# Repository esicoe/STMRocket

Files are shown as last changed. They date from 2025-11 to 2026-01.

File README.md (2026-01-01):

# STMRocket (KiCad v9.0)

> An open source model rocket flight computer with datalogging & parachute deploying capabilities.
> 
<br>

**This project was sponsored and made possible by PCBWay**




<br>

## Project Description

This is a personal project for an STM32 flight computer that will be flown on a high-power rocket to achieve the Level 1 high power rocketry certification in Canada.
<br>

## Capabilities

The computer is able to store flight data from its two sensors:

- ICM42670: 6-axis IMU with a gyroscope and accelerometer
- BME280: Pressure, temperature and humidity sensor

Data from the accelerometer and gyroscope is used to activate the pyro charge and release the rocket's parachute (single-deploy configuration).

Flight data is stored in a 4-megabyte flash memory chip and is offloaded from the computer using MicroSD.
<br>

During flight, the computer is powered by a 2S LiPo battery through an XT30 connector.

Programming interfaces: SWD and USB Micro-B.

<br>

For a more detailed overview of the components, consult the BOM and the KiCad schematic.

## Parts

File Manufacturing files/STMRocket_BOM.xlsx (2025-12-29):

 |  |  | xxxx xxxx xxxxx xxPCS BOM (Sample Bill of Materials)
Item # | *Designator | *Qty | Manufacturer | *Mfg Part # | Description / Value | *Package/Footprint | Type | Your Instructions / Notes
1 | U1 | 1 | ST | STM32F103C8T6 | IC MCU 32BIT 64KB FLASH 48LQFP | LQFP-48 | SMD
2 | U2 | 1 | InvenSense | ICM-42670-P | IMU ACCEL/GYRO/TEMP I2C/SPI | LGA-14 | SMD
3 | U3 | 1 | Bosch | BME280 | SENSOR PRESSURE HUMIDITY TEMP | LGA-8 | SMD
4 | U4 | 1 | Renesas | AT25SF041B-SSHD-T | IC FLASH 4MBIT SPI/QUAD 8SOIC | SOIC-8 | SMD
5 | U5 | 1 | Nexperia | PESD3V3S4UD,115 | TVS DIODE 3.3VWM 12VC 6TSOP | TSOP-6 | SMD
6 | U6 | 1 | Diodes | AP63203WU | IC REG BUCK 3.3V 2A TSOT23-6 | TSOT-23-6 | SMD
7 | U7, U8 | 2 | TI | ESD122DMXR | TVS DIODE 3.6VWM 8.4VC 3X2SON | SON-6 | SMD
8 | U9 | 1 | Diodes | AZ1117CH2-3.3 | IC REG LINEAR 3.3V 1A SOT-223-3 | SOT-223-3 | SMD
9 | Y1 | 1 | ECS | ECS-2520MV-160-CN-TR | OSC XO 16.0000MHZ CMOS SMD | 4-SMD | SMD
10 | C1 | 1 | ChemiCon | EMVY350ARA470MF55G | CAP ALUM 47UF 20% 35V SMD | CP_Elec_6.3x5.2 | SMD
11 | C2,C3,C4 | 3 | TDK | C2012X5R1C106K085AC | CAP CER 10UF 16V X5R 0805 | 0805 | SMD
12 | C5,C6,C7,C8 | 4 | TDK | C1608X5R0J106K080AB | CAP CER 10UF 6.3V X5R 0603 | 0603 | SMD
13 | C9 | 1 | Samsung | CL10B225KP8NNNC | CAP CER 2.2UF 10V X7R 0603 | 0603 | SMD
14 | C10,C11,C12 | 3 | TDK | C1005X6S1C105K050EC | CAP CER 1UF 15V X6S 0402 | 0402 | SMD
15 | C13, C14, C15, C16, C17, C18, C19, C20, C21, C22, C23, C24, C25, C26, C27 | 15 | Samsung | CL10E104KC8VPNC | CAP CER 100NF 100V X8L 0603 | 0402 | SMD
16 | C28, C29 | 2 | Samsung | CL10B103KO8WPNC | CAP CER 10NF 16V X7R 0603 | 0402 | SMD
17 | D1 | 1 | Vishay | SMF5V0A-E3-08 | TVS DIODE 5VWM 9.2VC DO219AB | DO-219AB | SMD
18 | D2, D3, D4 | 3 | Littelfuse | SMF4L8.5AT1G | TVS DIODE 8.5VWM 14.4VC SOD123F | SOD-123F | SMD
19 | D5, D6 | 2 | Vishay | BZD27C3V6P-E3-08 | DIODE ZENER 3.6V 800MW DO219AB | DO-219AB | SMD
19 | D7 | 2 | Littelfuse | SMF3.3 | TVS DIODE 3.3VWM 6.8VC SOD123F | SOD-123F | SMD
20 | FB1 | 1 | Pulse | PE-0603PFB121ST | FERRITE BEAD 120 OHM 0603 1LN | 0603 | SMD
21 | J1 | 1 |  |  | XT30PW-M Horizontal Connector |  | DNS
22 | J2 | 1 | Amphenol | 10103594-0001LF | CONN RCPT USB2.0 MICRO B SMD R/A | USB Micro B | SMD
23 | J3 | 1 |  |  | Horizontal 01x02 Screw Terminal |  | DNS
24 | J4 | 1 |  |  | Horizontal 01x02 Pins |  | DNS
25 | J5 | 1 |  |  | Horizontal 01x04 Pins |  | DNS
26 | J6 | 1 | Wurth | 693072010801 | CONN MICRO SD CARD R/A SMD | MicroSD | SMD
27 | R1 | 1 | Yaego | RC0402FR-07100KL | RES 100K OHM 1% 1/16W 0402 | 0402 | SMD
28 | R2, R3, R4, R5, R6 | 5 | Yaego | RC0603FR-0710KL | RES 10K OHM 1% 1/10W 0603 | 0402 | SMD
29 | R7, R8 | 2 | Yaego | RC0402JR-074K7L | RES 4.7K OHM 5% 1/16W 0402 | 0402 | SMD
30 | R9 | 1 | Panasonic | ERA-2AEB152X | RES SMD 1.5K OHM 0.1% 1/16W 0402 | 0402 | SMD
31 | R10 | 1 | Caddock | MP930-2.00-1% | RES 2 OHM 1% 30W TO220 | TO-220 | DNS

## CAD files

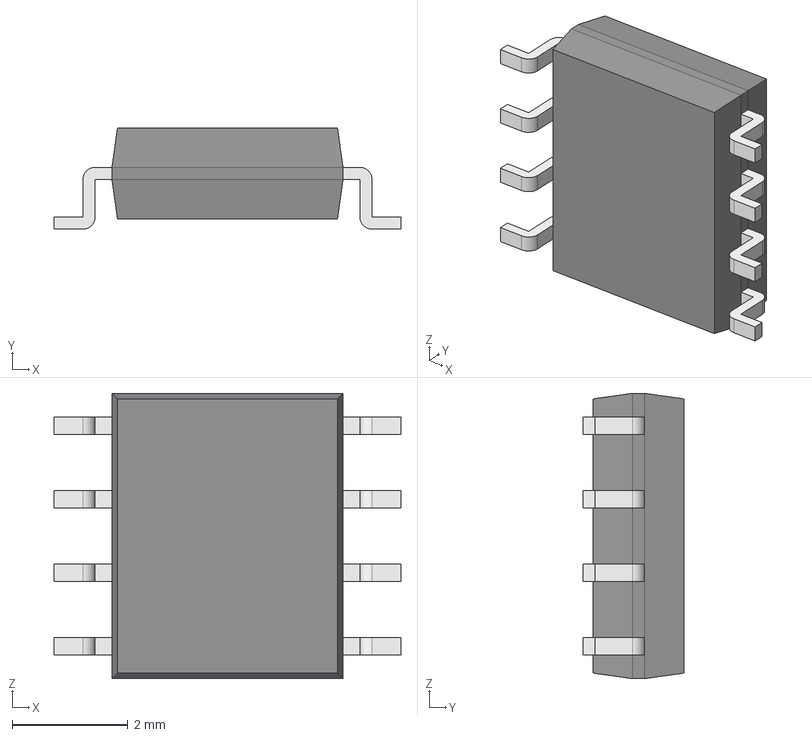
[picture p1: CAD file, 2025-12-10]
EDA files/EDA libraries/AT25SF041B-SSHD-T/AT25SF041B-SSHD-T.step
5.99 x 1.75 x 4.92 mm
Body001 (Mirror #1) x 4
XY-plane x 12
X-axis x 12

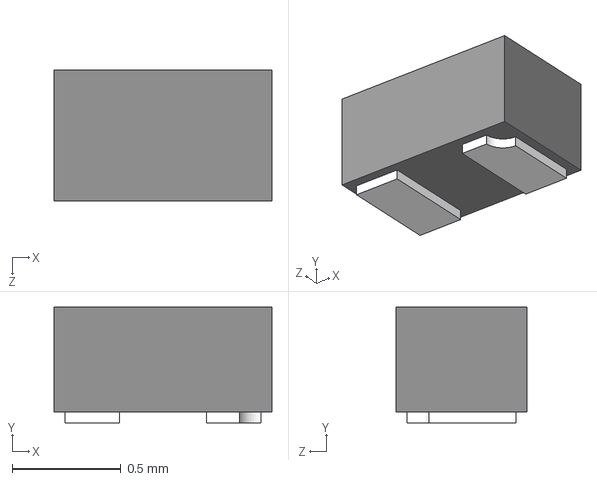
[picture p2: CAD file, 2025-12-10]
EDA files/EDA libraries/D12V0H1U2LP-7B/D12V0H1U2LP-7B.step
1.00 x 0.53 x 0.6 mm

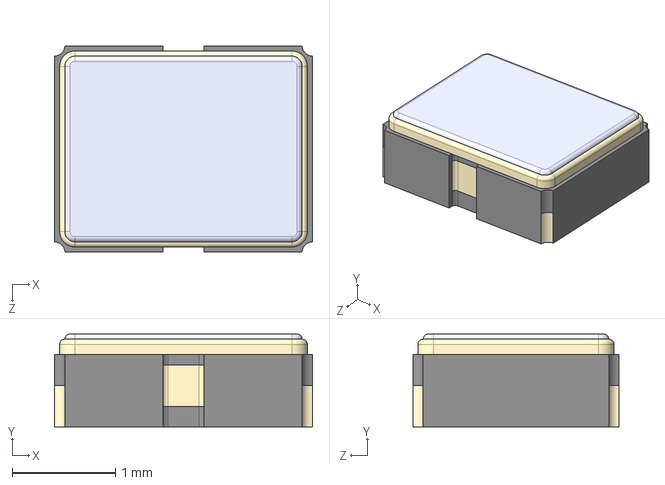
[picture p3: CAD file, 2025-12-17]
EDA files/EDA libraries/ECS-2520MV-160-CN-TR/ECS-2520MV-160-CN-TR.STEP
2.50 x 0.9 x 2.00 mm

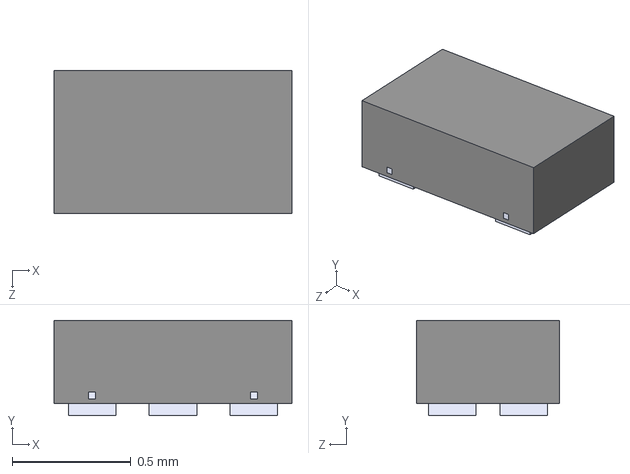
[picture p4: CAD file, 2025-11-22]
EDA files/EDA libraries/ESD122DMXR/ESD122DMXR.step
1.00 x 0.4 x 0.6 mm

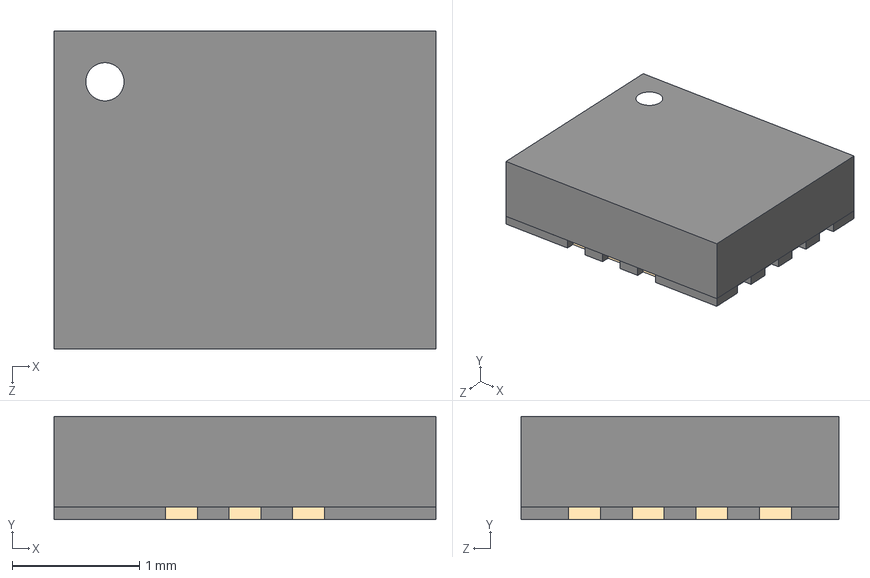
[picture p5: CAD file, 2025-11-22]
EDA files/EDA libraries/ICM_42670_P/ICM-42670-P.step
3.00 x 0.81 x 2.50 mm

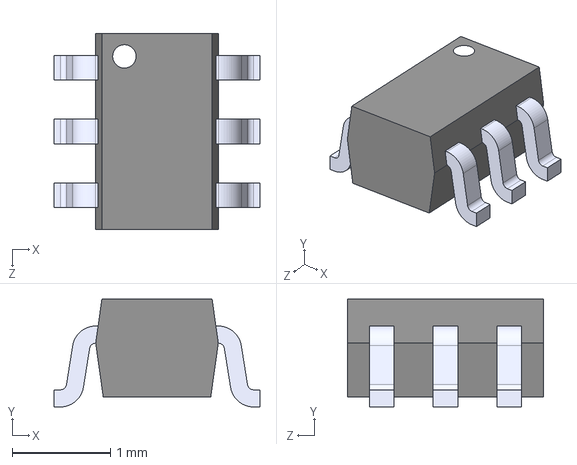
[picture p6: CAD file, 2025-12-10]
EDA files/EDA libraries/PESD3V3S5UD/PESD3V3S5UD.step
2.10 x 1.10 x 2.00 mm

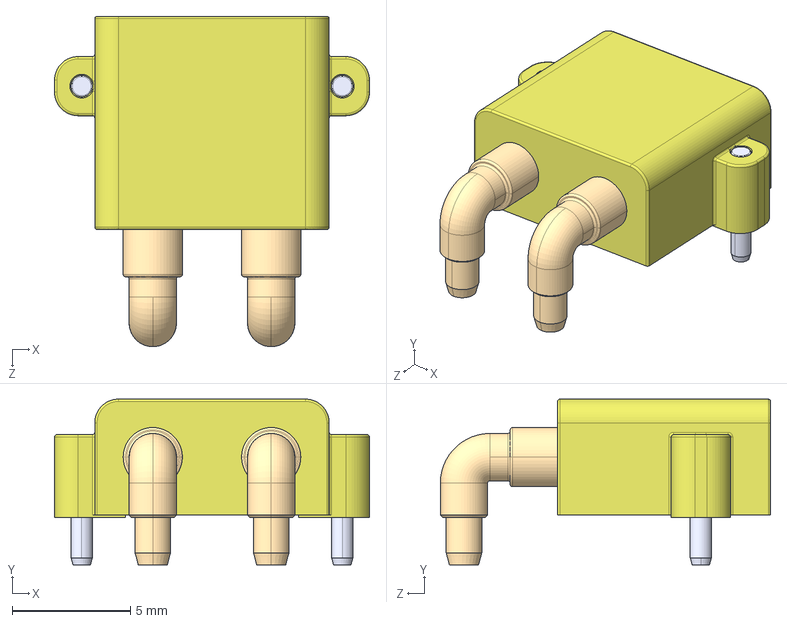
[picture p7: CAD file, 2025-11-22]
EDA files/EDA libraries/XT30PW-M/XT30PW-M--3DModel-STEP-269445.STEP
13.3 x 7.00 x 14.0 mm

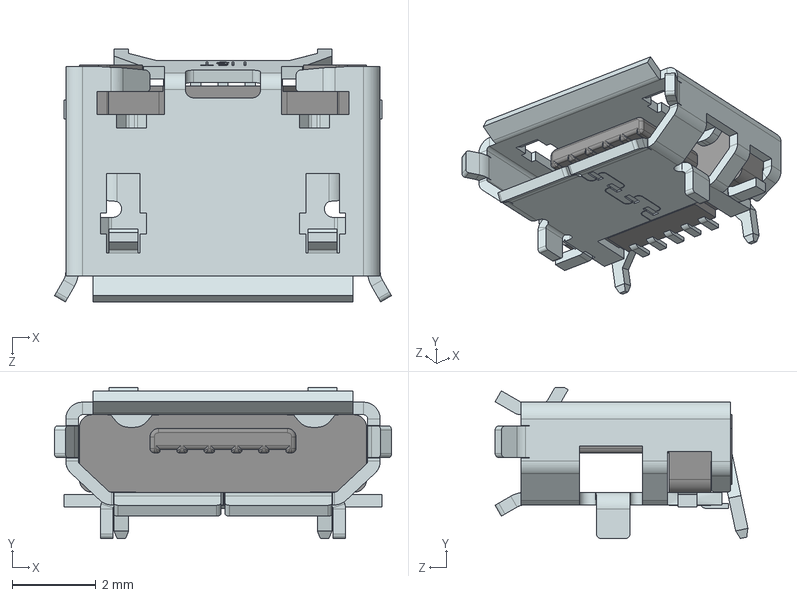
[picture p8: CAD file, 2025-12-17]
EDA files/EDA libraries/10103594-0001LF/10103594-0001LF--3DModel-STEP-269445.STEP
8.04 x 3.60 x 6.03 mm

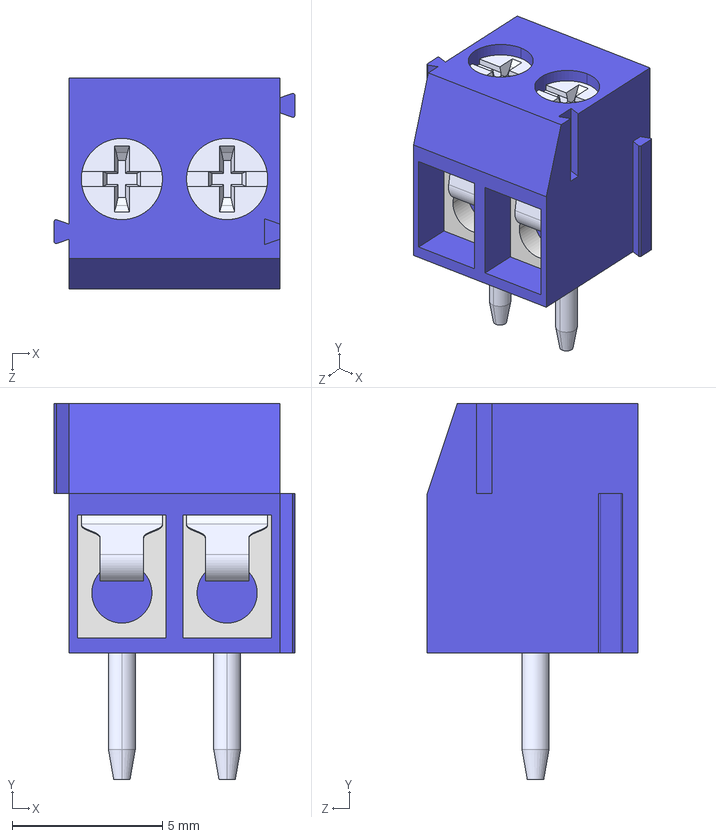
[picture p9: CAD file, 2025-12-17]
EDA files/EDA libraries/1776275-2/1776275-2--3DModel-STEP-510211.STEP
8.00 x 12.5 x 7.00 mm

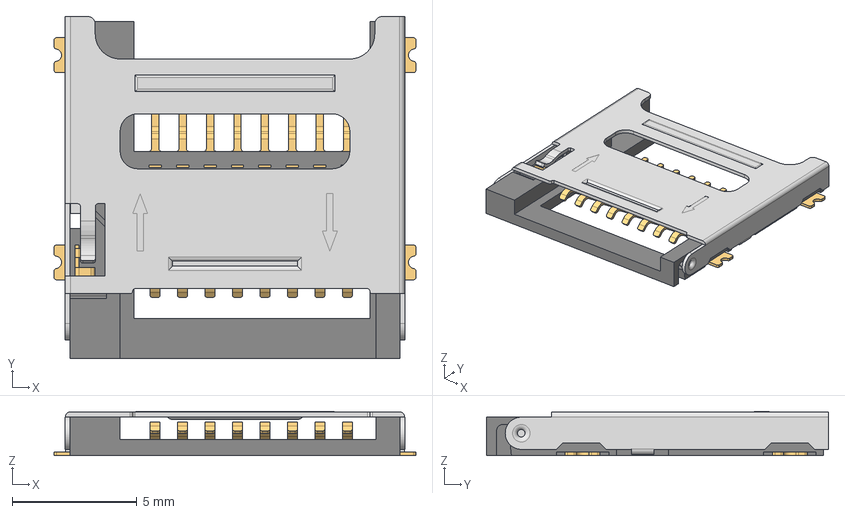
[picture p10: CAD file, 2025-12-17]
EDA files/EDA libraries/693072010801/693072010801+%28rev1%29.stp
14.5 x 13.7 x 1.77 mm
693072010801_PIN x 8
693072010801_PATTE x 3
693072010801_CACHE
693072010801_PATTE_SPE

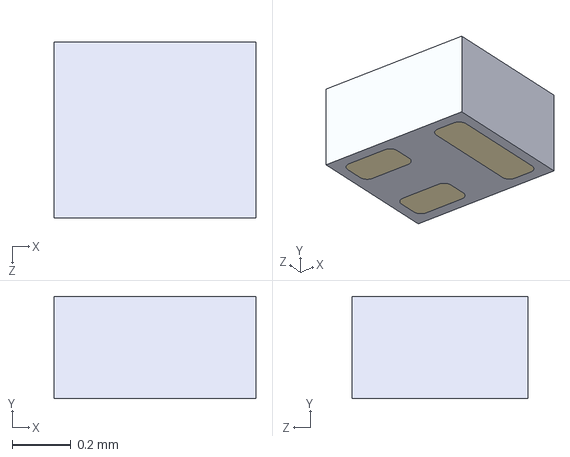
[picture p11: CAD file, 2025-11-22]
EDA files/EDA libraries/CSD23280F3/CSD23280F3.step
0.69 x 0.35 x 0.6 mm

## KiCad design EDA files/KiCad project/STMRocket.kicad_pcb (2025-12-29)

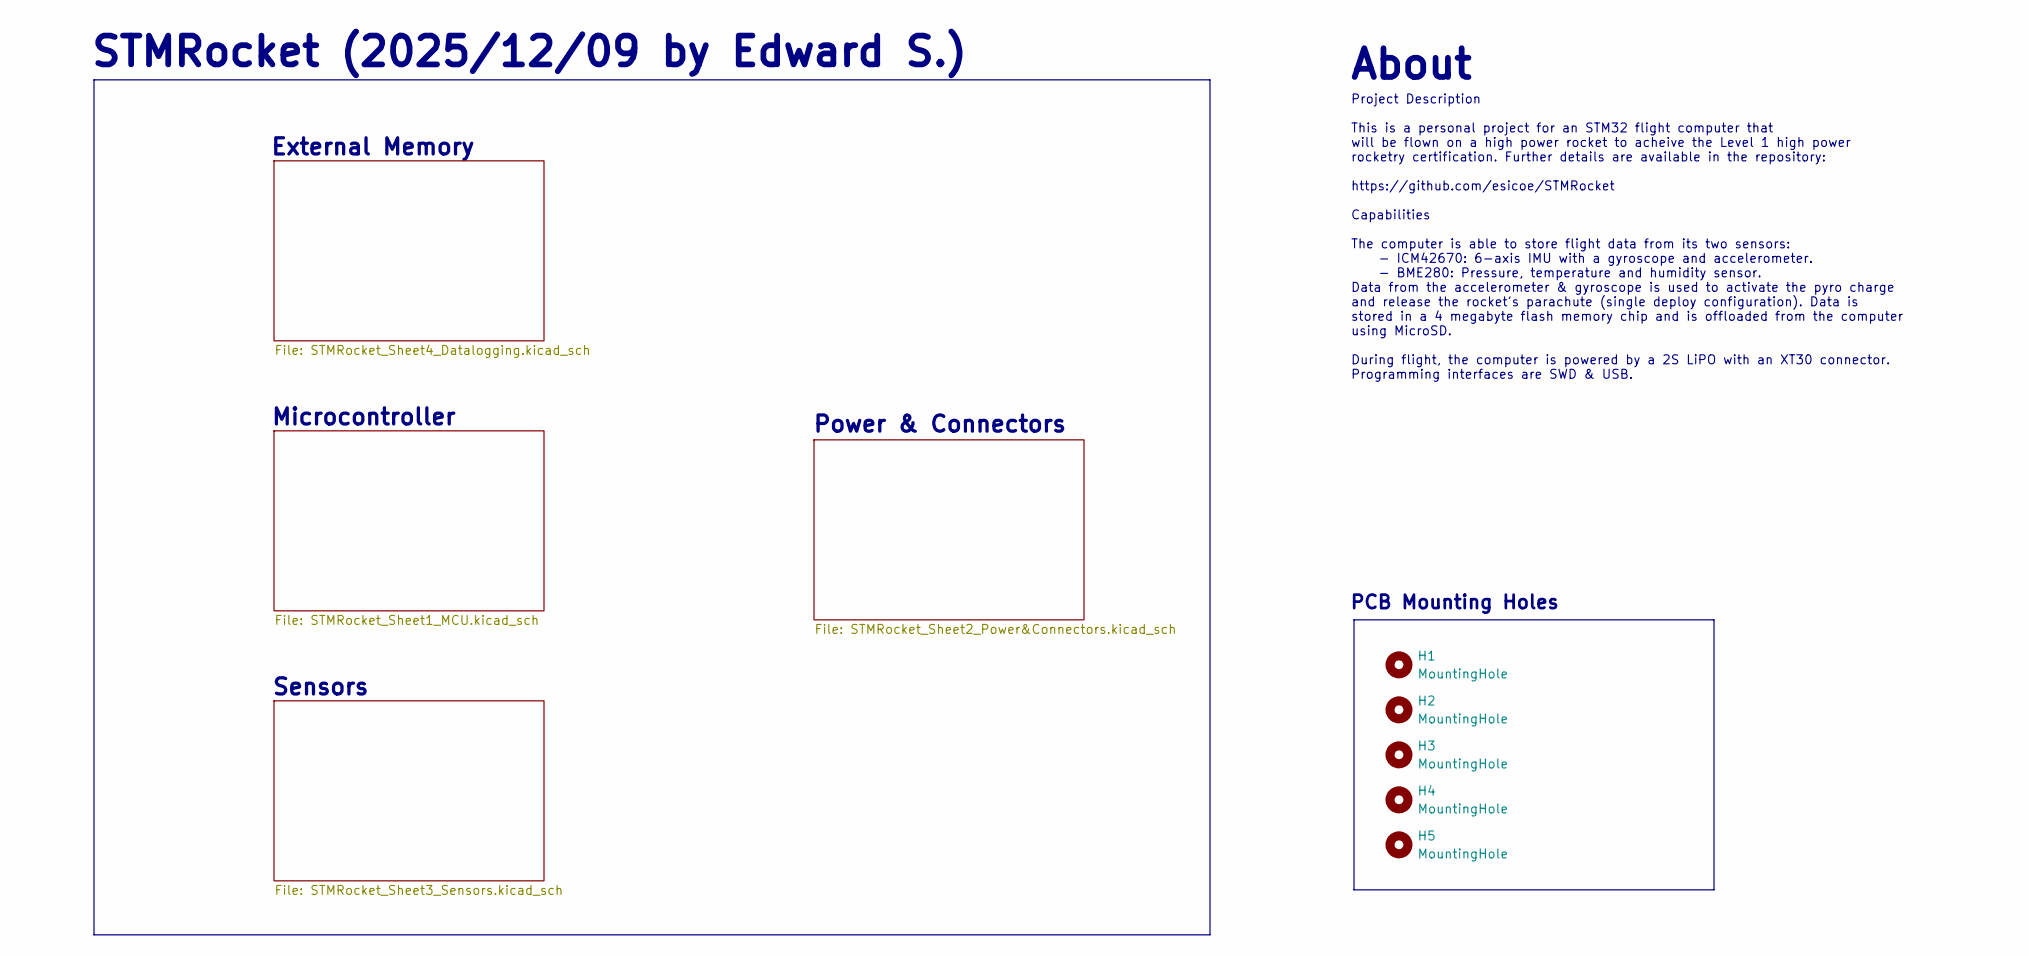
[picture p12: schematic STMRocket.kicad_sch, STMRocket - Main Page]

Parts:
H1, H2, H3, H4, H5: MountingHole; MountingHole_2.2mm_M2

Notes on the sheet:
PCB Mounting Holes
STMRocket (2025/12/09 by Edward S.)
Project Description This is a personal project for an STM32 flight computer that will be flown on a high power rocket to acheive the Level 1 high power rocketry certification. Further details are available in the repository: https://github.com/esicoe/STMRocket Capabilities The computer is able to s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
About
Sensors
External Memory
Microcontroller
Power & Connectors

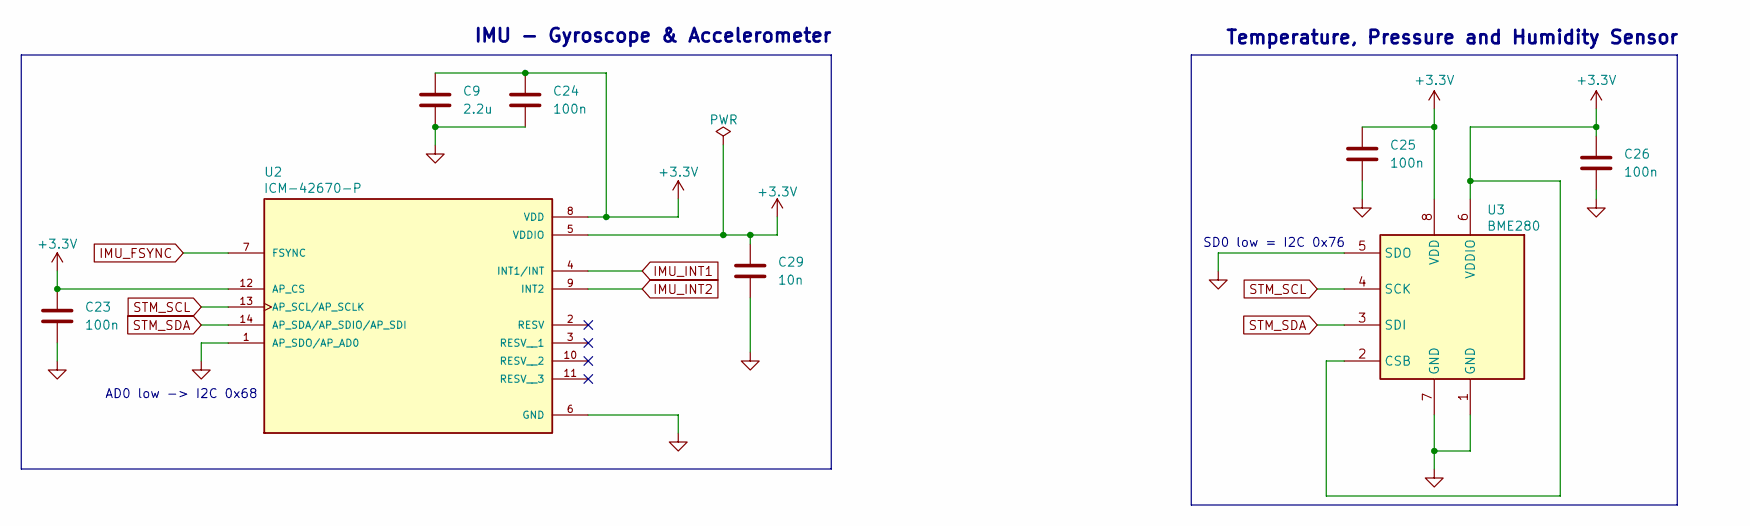
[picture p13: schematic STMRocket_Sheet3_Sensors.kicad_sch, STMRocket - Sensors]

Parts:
C9: 2.2u; C_0603_1608Metric
C23, C24, C25, C26: 100n; C_0402_1005Metric
C29: 10n; C_0402_1005Metric
U2: ICM-42670-P; LGA-14_3x2.5mm_P0.5mm_LayoutBorder3x4y; PARTREV 1.1
U3: BME280; Bosch_LGA-8_2.5x2.5mm_P0.65mm_ClockwisePinNumbering

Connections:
+3.3V: C9.1, C23.1, C24.1, C25.1, C26.1, C29.1, U2.5 (VDDIO), U2.8 (VDD), U2.12 (AP_CS), U3.2 (CSB), U3.6 (VDDIO), U3.8 (VDD); also elsewhere on the board
GND: C9.2, C23.2, C24.2, C25.2, C26.2, C29.2, U2.1 (AP_SDO/AP_AD0), U2.6 (GND), U3.1 (GND), U3.5 (SDO), U3.7 (GND); also elsewhere on the board
IMU_FSYNC: U2.7 (FSYNC); also elsewhere on the board
IMU_INT1: U2.4 (INT1/INT); also elsewhere on the board
IMU_INT2: U2.9 (INT2); also elsewhere on the board
STM_SCL: U2.13 (AP_SCL/AP_SCLK), U3.4 (SCK); also elsewhere on the board
STM_SDA: U2.14 (AP_SDA/AP_SDIO/AP_SDI), U3.3 (SDI); also elsewhere on the board

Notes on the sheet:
Temperature, Pressure and Humidity Sensor
IMU - Gyroscope & Accelerometer
AD0 low -> I2C 0x68
SD0 low = I2C 0x76

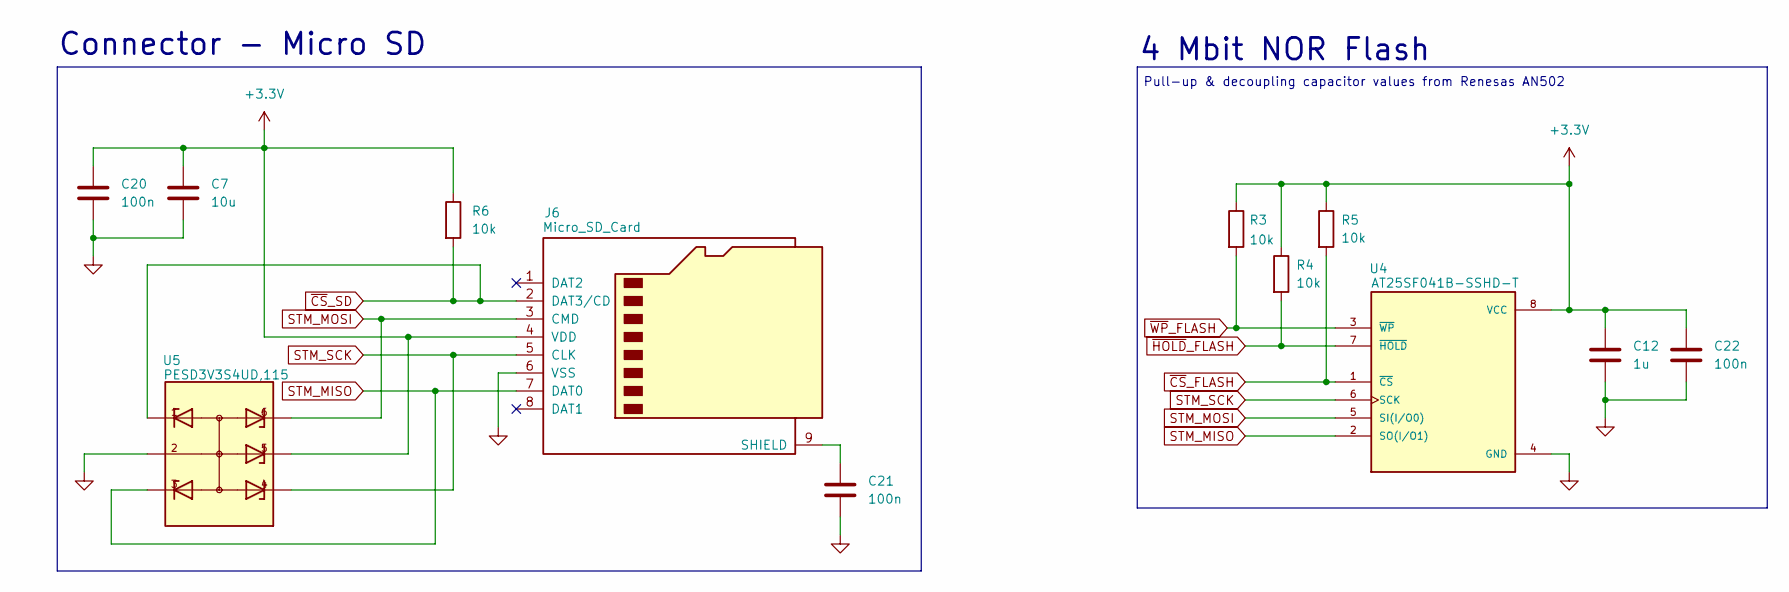
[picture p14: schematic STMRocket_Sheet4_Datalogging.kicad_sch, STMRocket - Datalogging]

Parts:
C7: 10u; C_0603_1608Metric
C12: 1u; C_0402_1005Metric
C20, C21, C22: 100n; C_0402_1005Metric
J6: Micro_SD_Card; microSD_HC_Wuerth_693072010801
R3, R4, R5, R6: 10k; R_0402_1005Metric
U4: AT25SF041B-SSHD-T; SOIC-8_3.9x4.9mm_P1.27mm; PARTREV G
U5: PESD3V3S4UD,115; SC-74-6_1.55x2.9mm_P0.95mm

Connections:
+3.3V: C7.1, C12.1, C20.1, C22.1, J6.4 (VDD), R3.1, R4.1, R5.1, R6.1, U4.8 (VCC), U5.5; also elsewhere on the board
GND: C7.2, C12.2, C20.2, C21.2, C22.2, J6.6 (VSS), U4.4 (GND), U5.2; also elsewhere on the board
unnamed: C21.1, J6.9 (SHIELD)
STM_MISO: J6.7 (DAT0), U4.2 (SO(I/O1)), U5.3; also elsewhere on the board
STM_MOSI: J6.3 (CMD), U4.5 (SI(I/O0)), U5.6; also elsewhere on the board
STM_SCK: J6.5 (CLK), U4.6 (SCK), U5.4; also elsewhere on the board
~CS_FLASH: R5.2, U4.1 (~CS); also elsewhere on the board
~CS_SD: J6.2 (DAT3/CD), R6.2, U5.1; also elsewhere on the board
~HOLD_FLASH: R4.2, U4.7 (~HOLD); also elsewhere on the board
~WP_FLASH: R3.2, U4.3 (~WP); also elsewhere on the board

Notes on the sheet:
Pull-up & decoupling capacitor values from Renesas AN502
4 Mbit NOR Flash
Connector - Micro SD

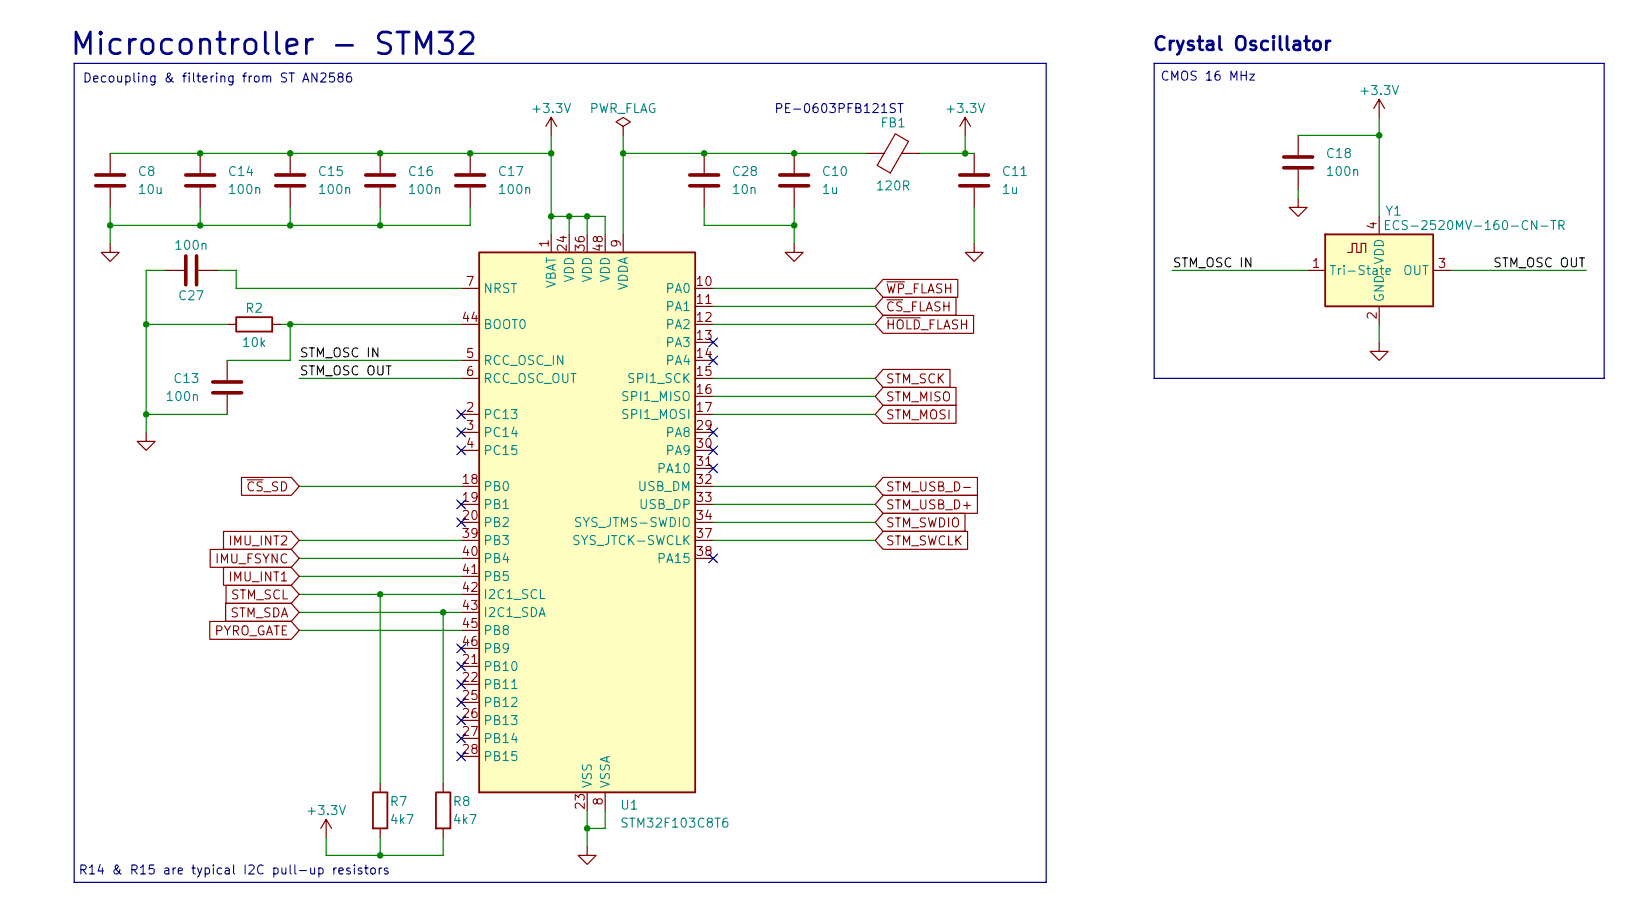
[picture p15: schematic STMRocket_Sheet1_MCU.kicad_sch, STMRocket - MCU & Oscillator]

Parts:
C8: 10u; C_0603_1608Metric
C10, C11: 1u; C_0402_1005Metric
C13, C14, C15, C16, C17, C18, C27: 100n; C_0402_1005Metric
C28: 10n; C_0402_1005Metric
FB1: 120R; L_0603_1608Metric
R2: 10k; R_0402_1005Metric
R7, R8: 4k7; R_0402_1005Metric
U1: STM32F103C8T6; LQFP-48_7x7mm_P0.5mm
Y1: ECS-2520MV-160-CN-TR; Oscillator_SMD_ECS_2520MV-xxx-xx-4Pin_2.5x2.0mm

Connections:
+3.3V: C8.1, C11.1, C14.1, C15.1, C16.1, C17.1, C18.1, FB1.2, R7.2, R8.2, U1.1 (VBAT), U1.24 (VDD), U1.36 (VDD), U1.48 (VDD), Y1.4 (VDD); also elsewhere on the board
/MCU/STM_OSC IN: U1.5 (RCC_OSC_IN), Y1.1 (Tri-State)
/MCU/STM_OSC OUT: U1.6 (RCC_OSC_OUT), Y1.3 (OUT)
GND: C8.2, C10.2, C11.2, C13.2, C14.2, C15.2, C16.2, C17.2, C18.2, C27.1, C28.2, R2.1, U1.8 (VSSA), U1.23 (VSS), U1.35 (VSS), U1.47 (VSS), Y1.2 (GND); also elsewhere on the board
IMU_FSYNC: U1.40 (PB4); also elsewhere on the board
IMU_INT1: U1.41 (PB5); also elsewhere on the board
IMU_INT2: U1.39 (PB3); also elsewhere on the board
unnamed: C13.1, R2.2, U1.44 (BOOT0)
unnamed: C27.2, U1.7 (NRST)
unnamed: C10.1, C28.1, FB1.1, U1.9 (VDDA)
PYRO_GATE: U1.45 (PB8); also elsewhere on the board
STM_MISO: U1.16 (SPI1_MISO); also elsewhere on the board
STM_MOSI: U1.17 (SPI1_MOSI); also elsewhere on the board
STM_SCK: U1.15 (SPI1_SCK); also elsewhere on the board
STM_SCL: R7.1, U1.42 (I2C1_SCL); also elsewhere on the board
STM_SDA: R8.1, U1.43 (I2C1_SDA); also elsewhere on the board
STM_SWCLK: U1.37 (SYS_JTCK-SWCLK); also elsewhere on the board
STM_SWDIO: U1.34 (SYS_JTMS-SWDIO); also elsewhere on the board
STM_USB_D+: U1.33 (USB_DP); also elsewhere on the board
STM_USB_D-: U1.32 (USB_DM); also elsewhere on the board
~CS_FLASH: U1.11 (PA1); also elsewhere on the board
~CS_SD: U1.18 (PB0); also elsewhere on the board
~HOLD_FLASH: U1.12 (PA2); also elsewhere on the board
~WP_FLASH: U1.10 (PA0); also elsewhere on the board

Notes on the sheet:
Decoupling & filtering from ST AN2586
CMOS 16 MHz
PE-0603PFB121ST
R14 & R15 are typical I2C pull-up resistors
Microcontroller - STM32
Crystal Oscillator

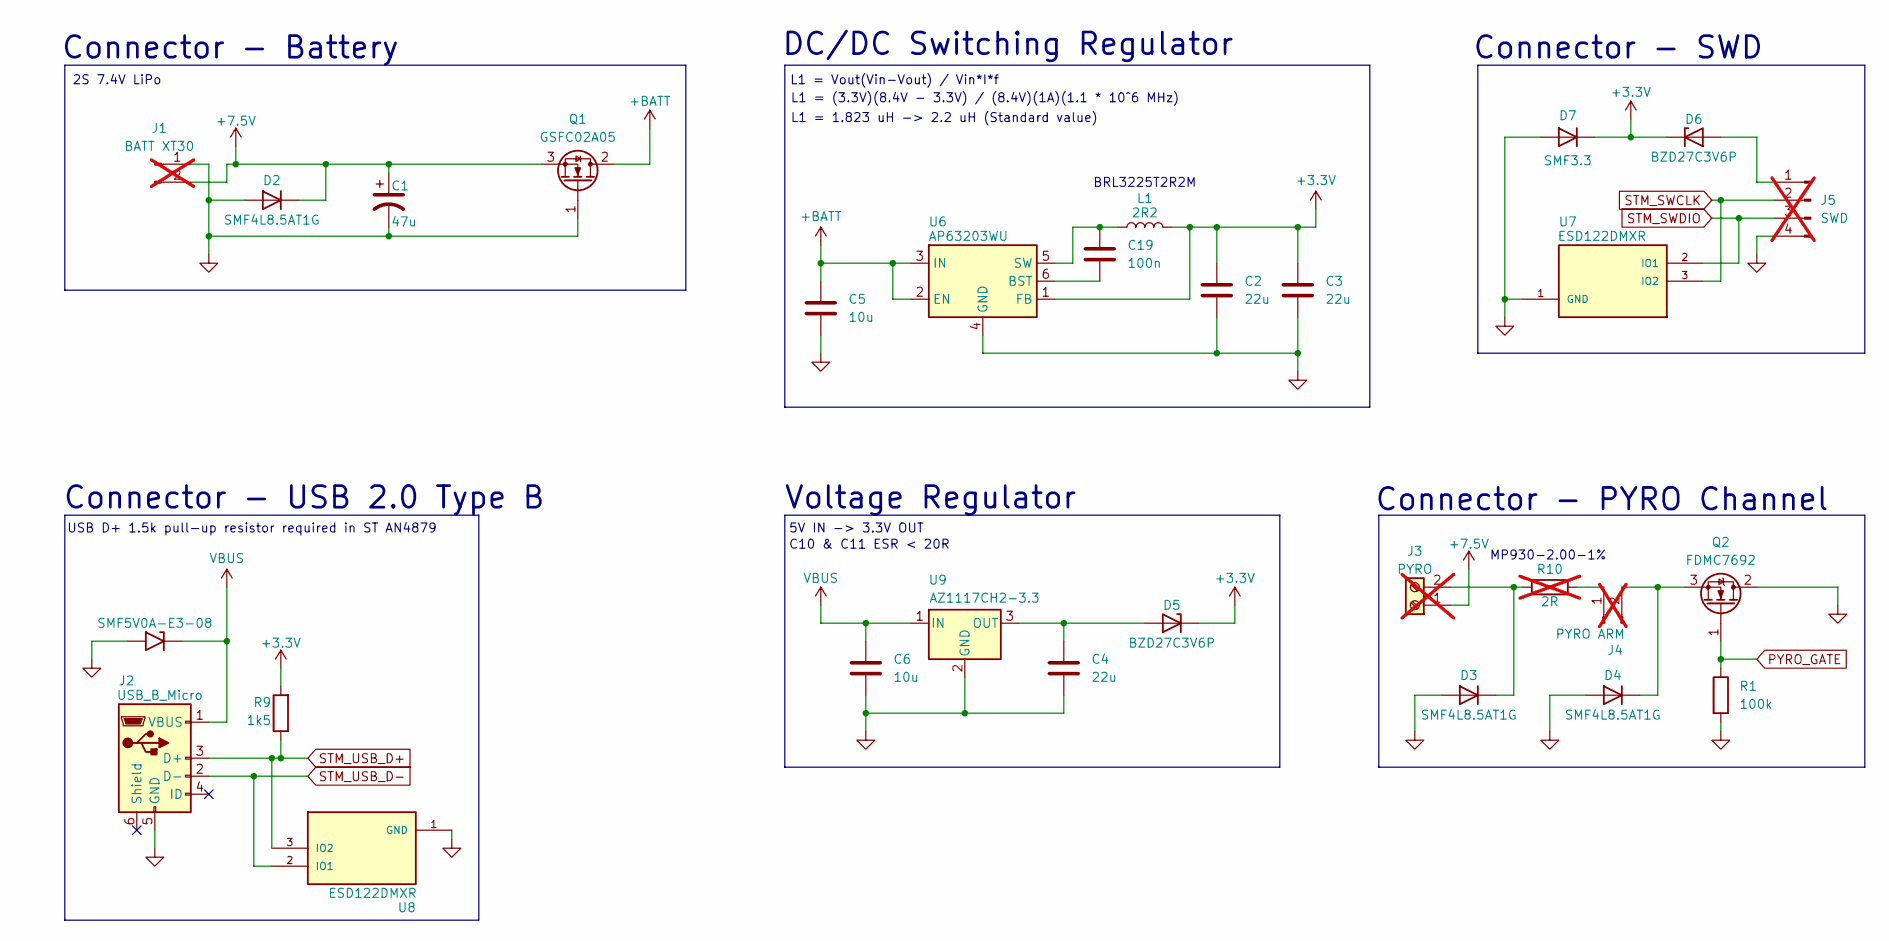
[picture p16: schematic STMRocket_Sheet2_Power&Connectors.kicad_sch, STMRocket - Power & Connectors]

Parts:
C1: 47u; CP_Elec_6.3x5.2
C2, C3, C4: 22u; C_0805_2012Metric
C5, C6: 10u; C_0603_1608Metric
C19: 100n; C_0402_1005Metric
D1: SMF5V0A-E3-08; D_SMF
D2, D3, D4: SMF4L8.5AT1G; D_SOD-123F
D5, D6: BZD27C3V6P; D_SMF
D7: SMF3.3; D_SOD-123F
J1: BATT XT30; AMASS_XT30PW-M_1x02_P2.50mm_Horizontal; not fitted
J2: USB_B_Micro; USB_Micro-B_Amphenol_10103594-0001LF_Horizontal
J3: PYRO; TerminalBlock_RND_205-00001_1x02_P5.00mm_Horizontal; not fitted
J4: PYRO ARM; PinHeader_1x02_P2.54mm_Vertical; not fitted
J5: SWD; PinHeader_1x04_P2.54mm_Vertical; not fitted
L1: 2R2; L_1210_3225Metric
Q1: GSFC02A05; SOT-23-3
Q2: FDMC7692; TO-252-2
R1: 100k; R_0402_1005Metric
R9: 1k5; R_0402_1005Metric
R10: 2R; TO-220-2_Horizontal_TabDown; not fitted
U6: AP63203WU; TSOT-23-6
U7, U8: ESD122DMXR; IC_ESD122DMXR; PARTREV A
U9: AZ1117CH2-3.3; SOT-223-3_TabPin2

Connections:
+3.3V: C2.1, C3.1, D5.1 (K), D6.1 (K), D7.1 (K), L1.2, R9.2, U6.1 (FB); also elsewhere on the board
+7.5V: C1.1, D2.1 (K), J1.2, J3.1, Q1.3 (S)
+BATT: C5.1, Q1.2 (D), U6.2 (EN), U6.3 (IN)
GND: C1.2, C2.2, C3.2, C4.2, C5.2, C6.2, D1.2 (A2), D2.2 (A), D3.2 (A), D4.2 (A), D7.2 (A), J1.1, J2.5 (GND), J5.4, Q1.1 (G), Q2.2 (D), R1.2, U6.4 (GND), U7.1 (GND), U8.1 (GND), U9.2 (GND); also elsewhere on the board
unnamed: D3.1 (K), J3.2, R10.2
unnamed: D4.1 (K), J4.2, Q2.3 (S)
unnamed: C4.1, D5.2 (A), U9.3 (OUT)
unnamed: D6.2 (A), J5.1
unnamed: J4.1, R10.1
unnamed: C19.2, U6.6 (BST)
unnamed: C19.1, L1.1, U6.5 (SW)
PYRO_GATE: Q2.1 (G), R1.1; also elsewhere on the board
STM_SWCLK: J5.2, U7.3 (IO2); also elsewhere on the board
STM_SWDIO: J5.3, U7.2 (IO1); also elsewhere on the board
STM_USB_D+: J2.3 (D+), R9.1, U8.3 (IO2); also elsewhere on the board
STM_USB_D-: J2.2 (D-), U8.2 (IO1); also elsewhere on the board
VBUS: C6.1, D1.1 (A1), J2.1 (VBUS), U9.1 (IN)

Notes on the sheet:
DC/DC Switching Regulator
Connector - Battery
MP930-2.00-1%
Voltage Regulator
Connector - USB 2.0 Type B
USB D+ 1.5k pull-up resistor required in ST AN4879
5V IN -> 3.3V OUT
L1 = 1.823 uH -> 2.2 uH (Standard value)
L1 = Vout(Vin-Vout) / Vin*I*f
2S 7.4V LiPo
C10 & C11 ESR < 20R
L1 = (3.3V)(8.4V - 3.3V) / (8.4V)(1A)(1.1 * 10^6 MHz)
Connector - PYRO Channel
Connector - SWD
BRL3225T2R2M

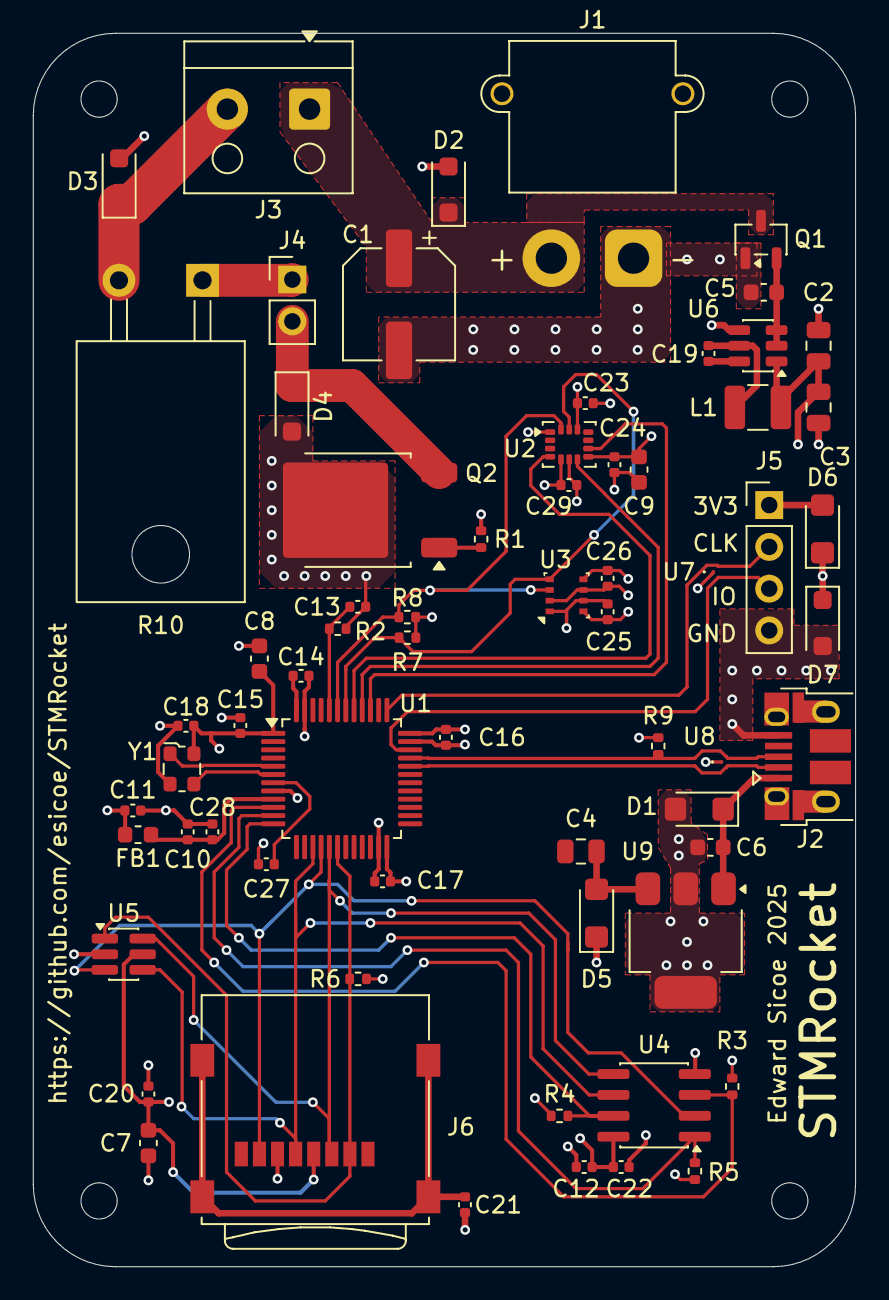
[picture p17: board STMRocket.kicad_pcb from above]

Board: 4 copper layers, 50.0 x 75.0 mm, 70 parts (0 on the bottom side), 35 nets.

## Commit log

2025-12-10 Datasheet renaming and schematic formatting, text, tables, etc.
    [KiCad Project.kicad_sch, STMRocket_Bill_of_materials.xlsx, STMRocket_Sheet1_MCU.kicad_sch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]
2025-12-13 Updated layout, documentation and schematic. Component placement finished.
    [HPRFC_Sheet1_MCU.kicad_sch, HPRFC_Sheet2_Power&Connectors.kicad_sch, HPRFC_Sheet3_Sensors.kicad_sch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]
2025-12-14 PCB update
    [KiCad Project.kicad_pcb, STMRocket_Sheet1_MCU.kicad_sch, STMRocket_Sheet2_Power&Connectors.kicad_sch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]
2025-12-15 finished pcb
    [KiCad Project.kicad_pcb, STMRocket_Sheet1_MCU.kicad_sch, STMRocket_Sheet2_Power&Connectors.kicad_sch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]
2025-12-27 pcb update and bom
    [STMRocket.kicad_pcb, STMRocket.kicad_sch, STMRocket_Sheet1_MCU.kicad_sch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]
2025-12-29 PCB finished
    [STMRocket.kicad_pcb]
2025-12-29 Final PCB revision
    [STMRocket.kicad_pcb]
2025-12-29 Final - PCB, Man. Files & BOM
    [STMRocket.kicad_pcb, STMRocket_BOM.xlsx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]
2025-12-29 Update project title to include KiCad version
2026-01-01 Update manufacturing files
    [STMRocket Drill.drl]
